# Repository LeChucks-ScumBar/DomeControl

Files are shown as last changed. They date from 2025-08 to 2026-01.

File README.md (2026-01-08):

# DomeControl
DomeControl for N.I.N.A
--------------------------

Kuppelsteuerung für das Großfeldteleskop in der Sternwarte Waldbröl (www.stsci.de)
------------------------
Status: Entwurf

anstehende Schritte:
 - Elektronik und Schalter montieren und anschließen
 - Test steurung mit N.I.N.A und Kuppel

 Software von:
 https://github.com/juanmb/ArduinoDomeController

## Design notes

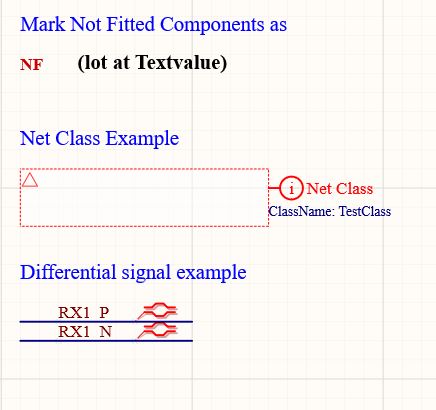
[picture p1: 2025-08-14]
Altium designe files/Bilder/Unbenannt.JPG

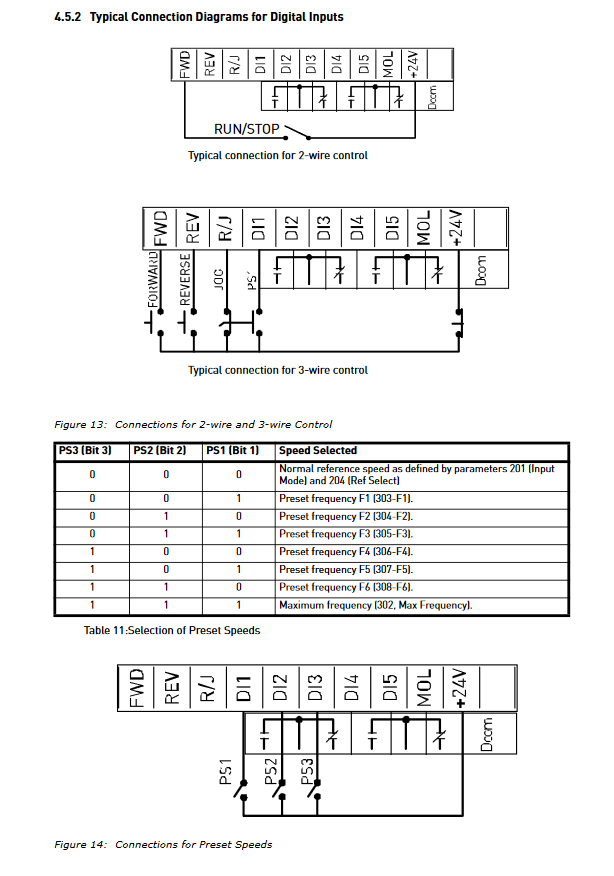
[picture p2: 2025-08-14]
Docs/Screenshot 2025-01-07 084854.png

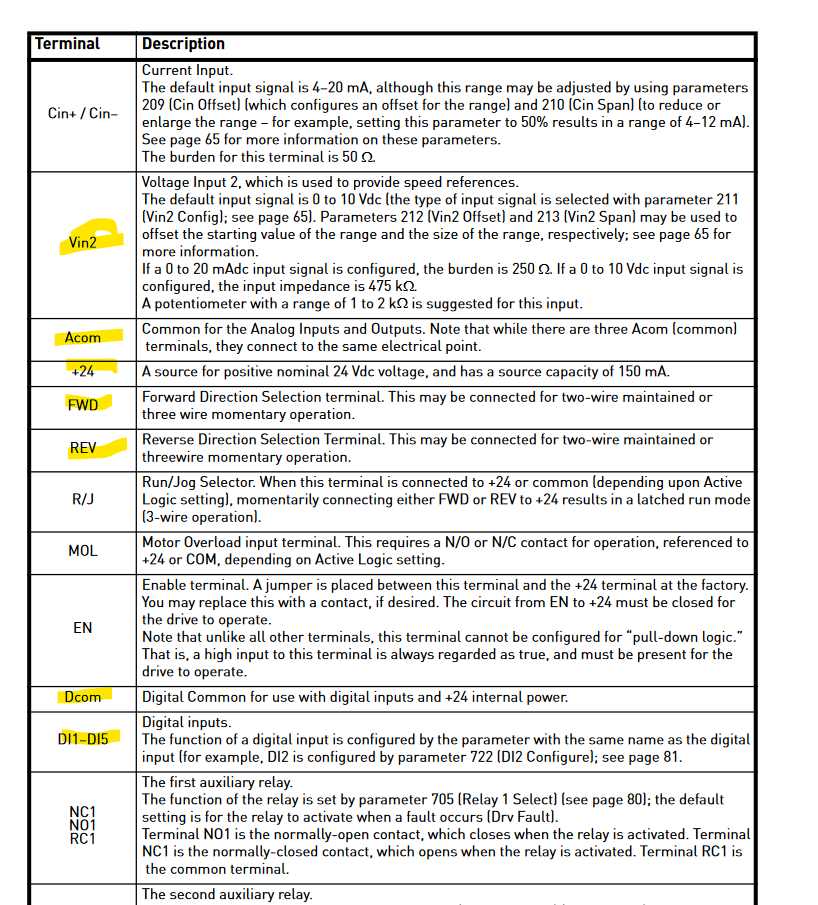
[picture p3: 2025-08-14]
Docs/Screenshot 2025-01-07 084709.png

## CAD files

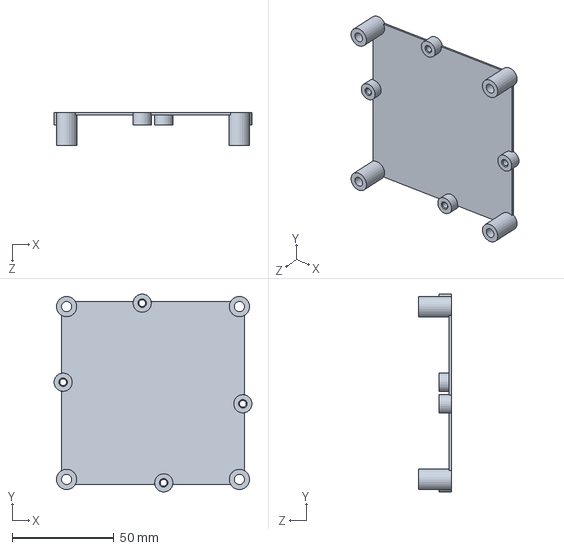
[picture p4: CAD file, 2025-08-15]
Solidworks/ArduinoBoxHalter/Case_oben.SLDPRT
97.4 x 97.4 x 16.0 mm

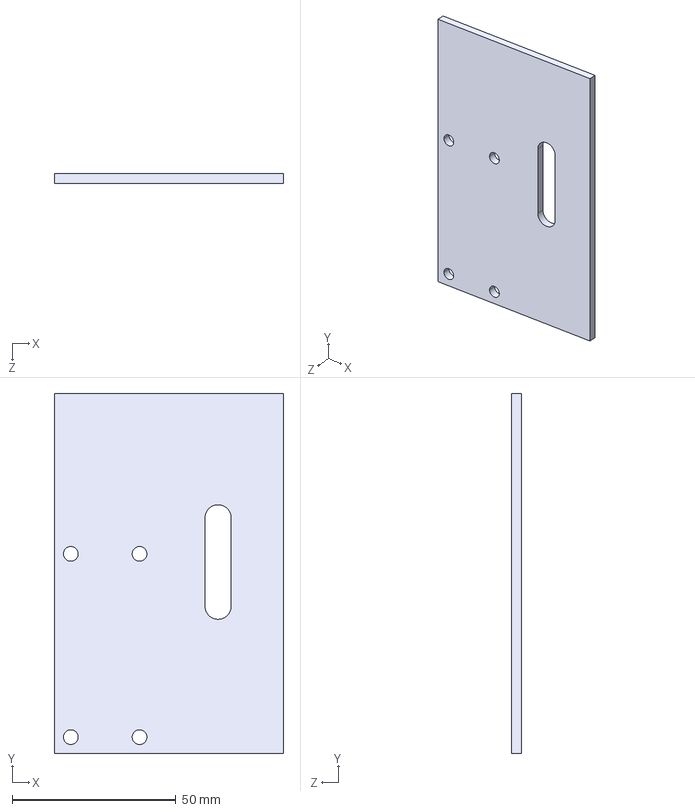
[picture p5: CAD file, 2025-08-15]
Solidworks/HomeTaster/HomeTaster.STEP
70.0 x 110.0 x 3.00 mm

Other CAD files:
Solidworks/ArduinoBoxHalter/Case_oben.STL
Solidworks/HomeTaster/HomeTaster.SLDDRW
Solidworks/HomeTaster/HomeTaster.SLDPRT

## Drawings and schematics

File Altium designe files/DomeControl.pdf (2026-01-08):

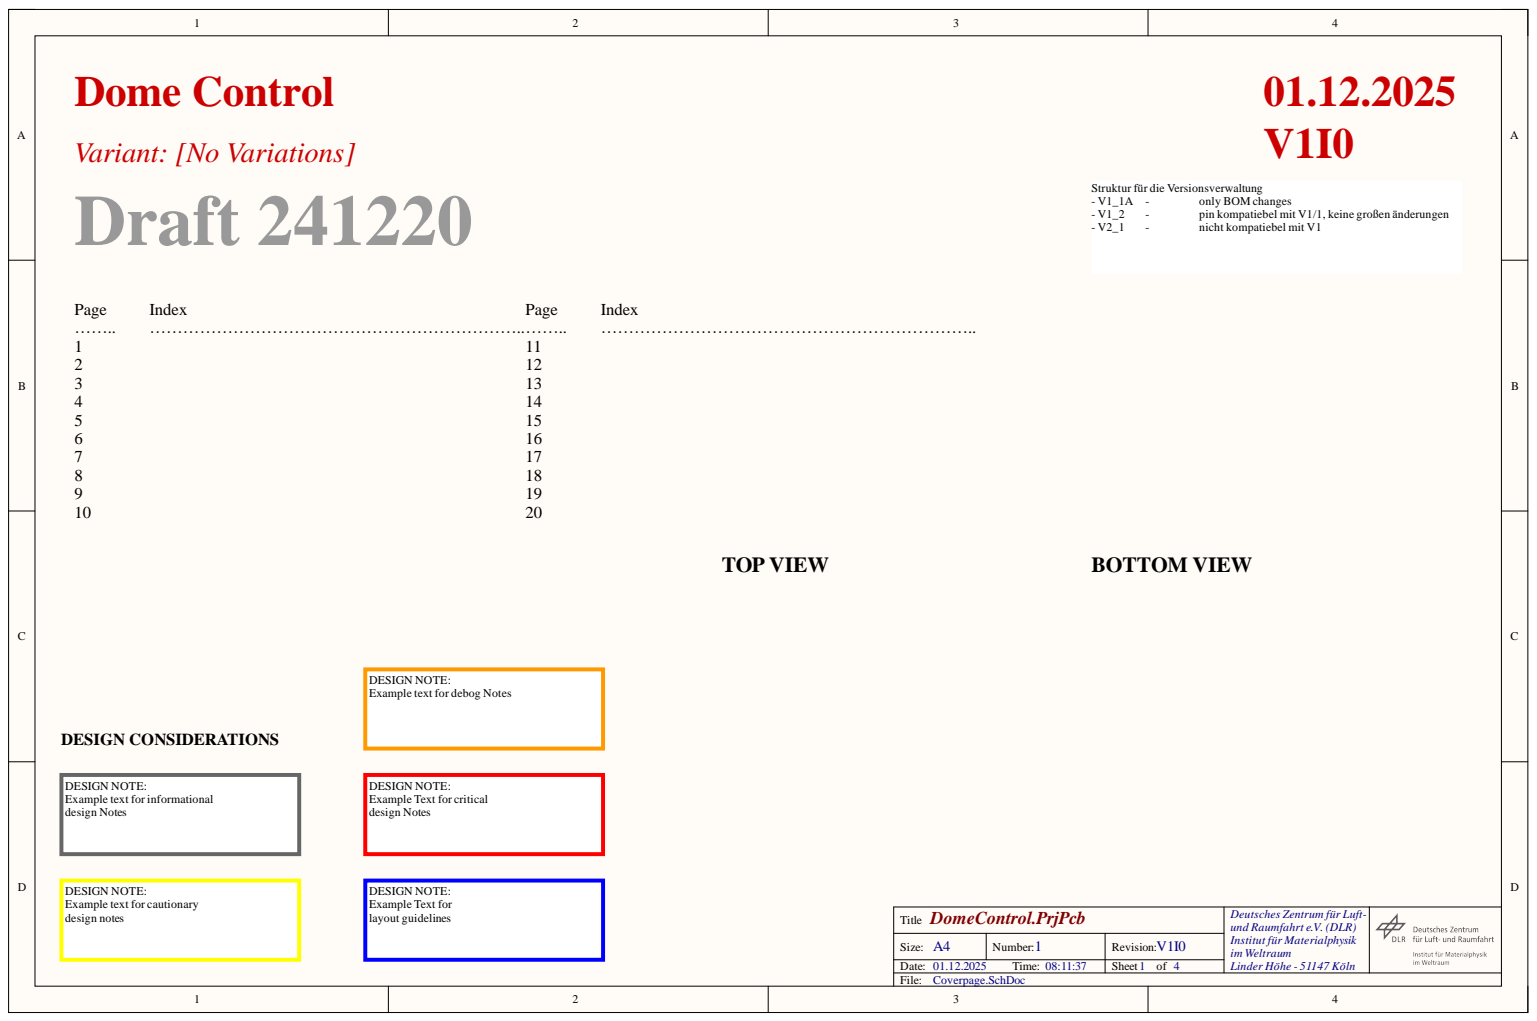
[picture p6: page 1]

Struktur für die Versionsverwaltung

DESIGN NOTE:
Example text for debog Notes

Example text for informational
design Notes

Example Text for critical

Example text for cautionary
design notes

Deutsches Zentrum für Luft-
und Raumfahrt e.V. (DLR)
Institut für Materialphysik
im Weltraum

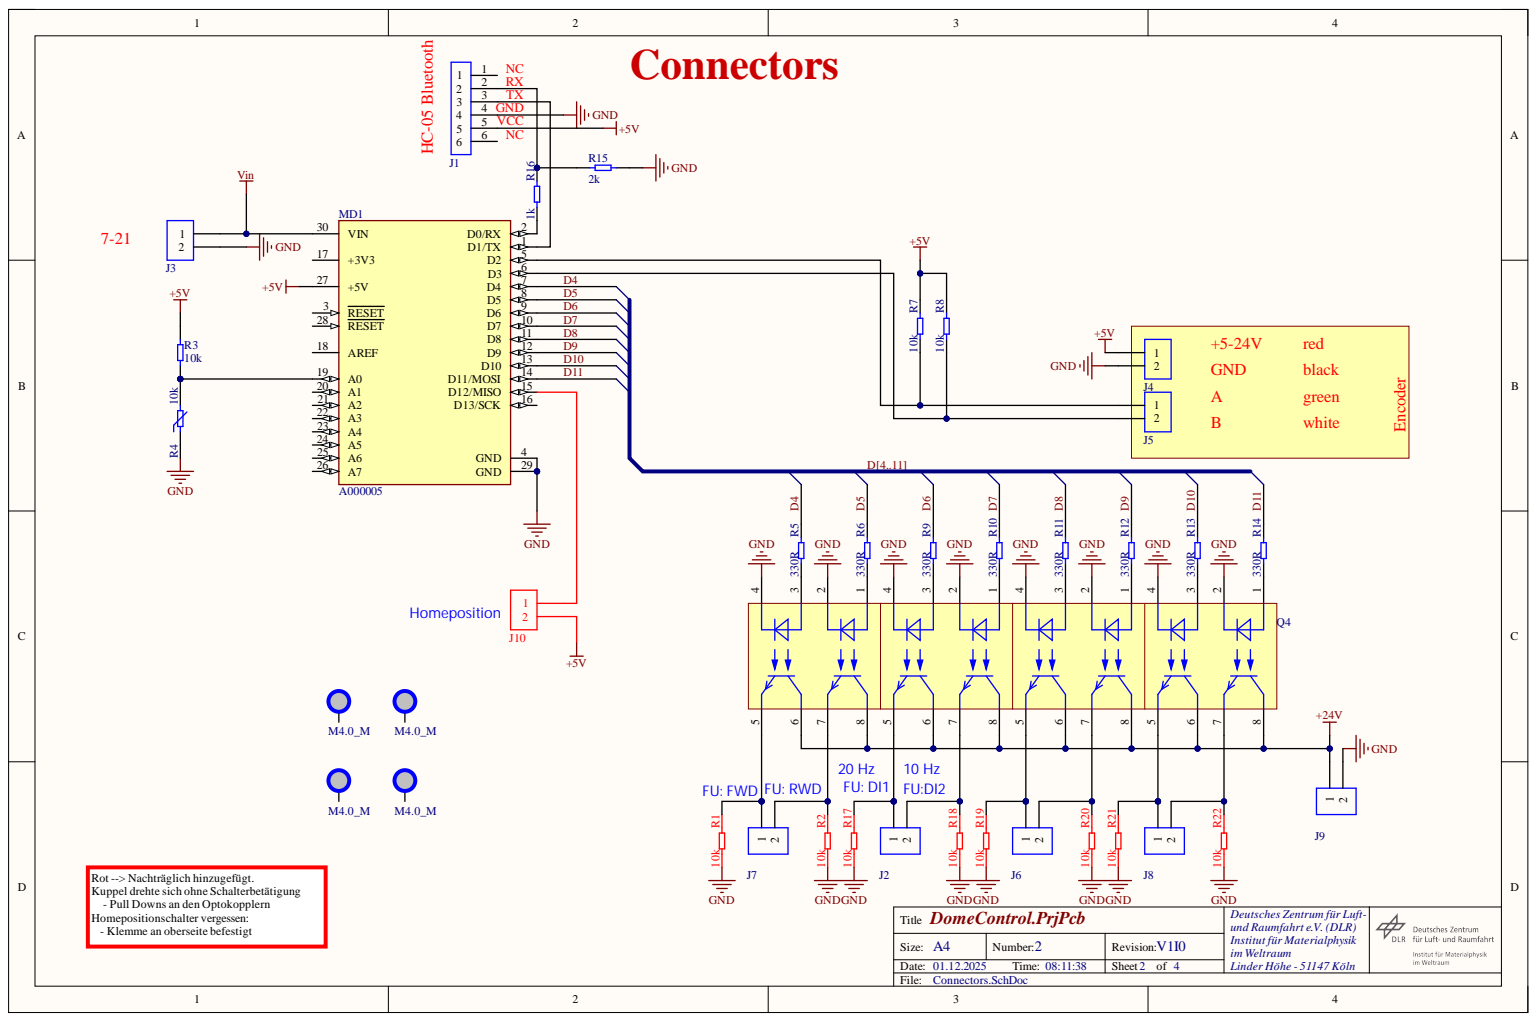
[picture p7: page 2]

Rot --> Nachträglich hinzugefügt.
Kuppel drehte sich ohne Schalterbetätigung
- Pull Downs an den Optokopplern
Homepositionschalter vergessen:
- Klemme an oberseite befestigt

Deutsches Zentrum für Luft-
und Raumfahrt e.V. (DLR)
Institut für Materialphysik
im Weltraum

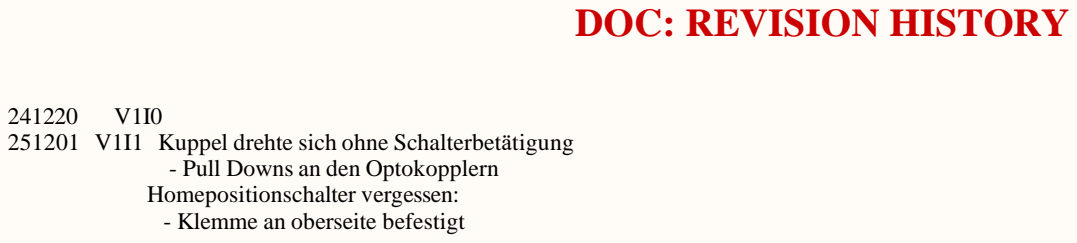
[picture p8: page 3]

251201 V1I1 Kuppel drehte sich ohne Schalterbetätigung

- Pull Downs an den Optokopplern
Homepositionschalter vergessen:
- Klemme an oberseite befestigt

Deutsches Zentrum für Luft-
und Raumfahrt e.V. (DLR)
Institut für Materialphysik
im Weltraum

DOC REVISION HISTORY.SchDoc

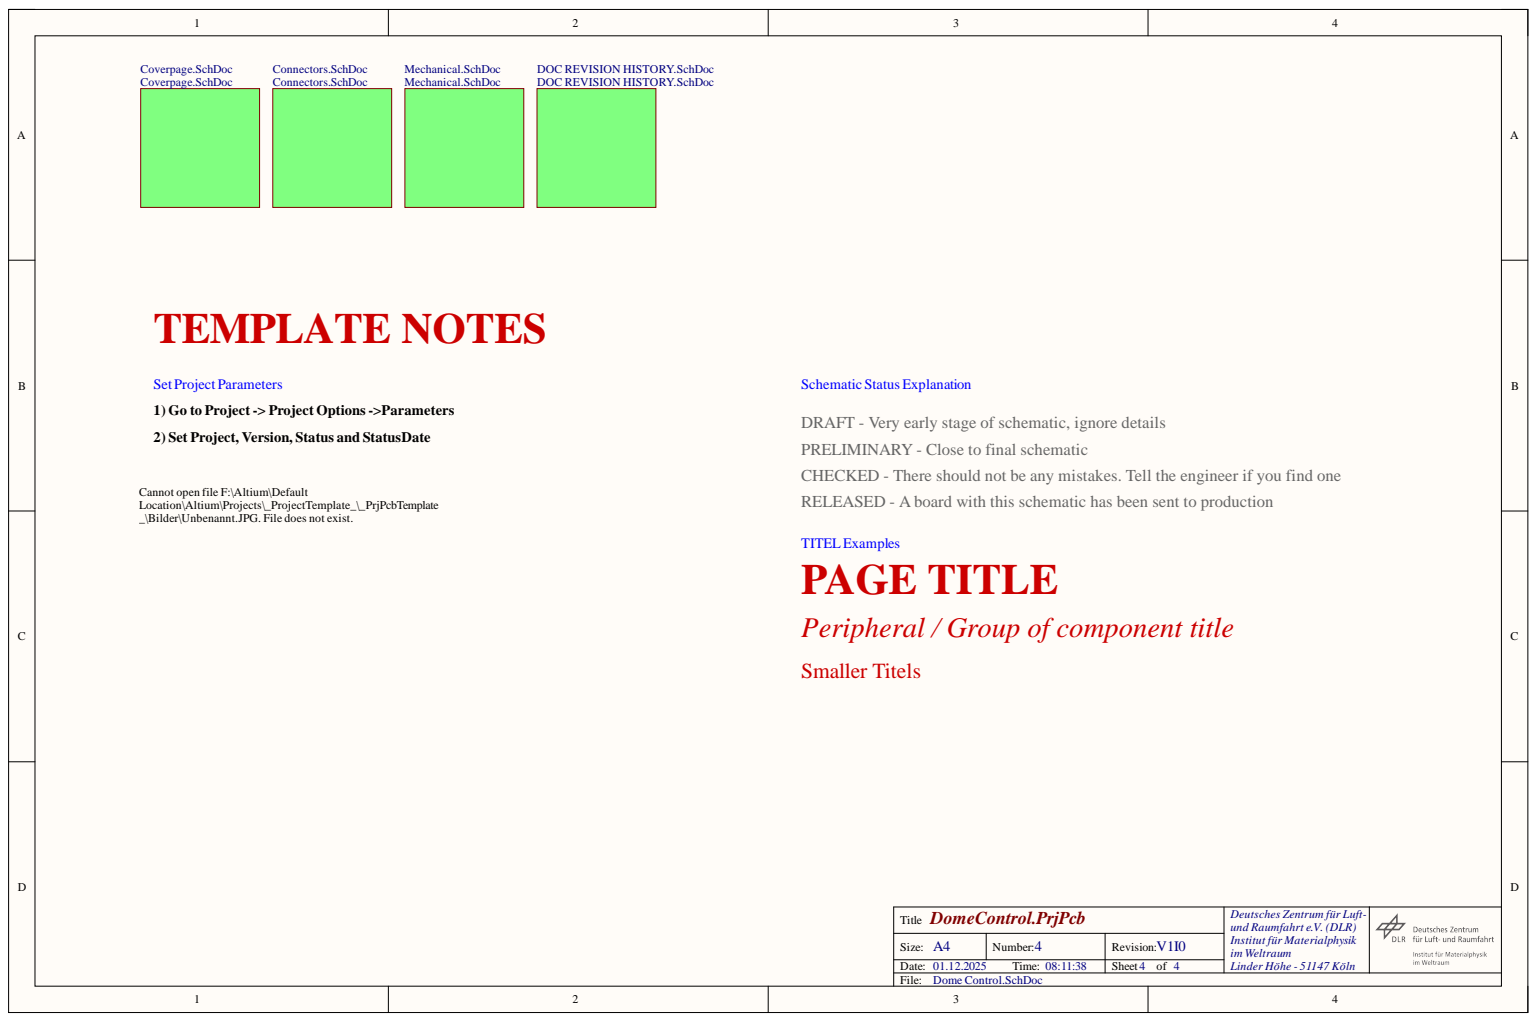
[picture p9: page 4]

DOC REVISION HISTORY.SchDoc

1) Go to Project -> Project Options ->Parameters

DRAFT - Very early stage of schematic, ignore details
PRELIMINARY - Close to final schematic
CHECKED - There should not be any mistakes. Tell the engineer if you find one

2) Set Project, Version, Status and StatusDate

RELEASED - A board with this schematic has been sent to production Cannot open file F:\Altium\Default
Location\Altium\Projects\_ProjectTemplate_\_PrjPcbTemplate
_\Bilder\Unbenannt.JPG. File does not exist.

Peripheral / Group of component title

Deutsches Zentrum für Luft-
und Raumfahrt e.V. (DLR)
Institut für Materialphysik
im Weltraum

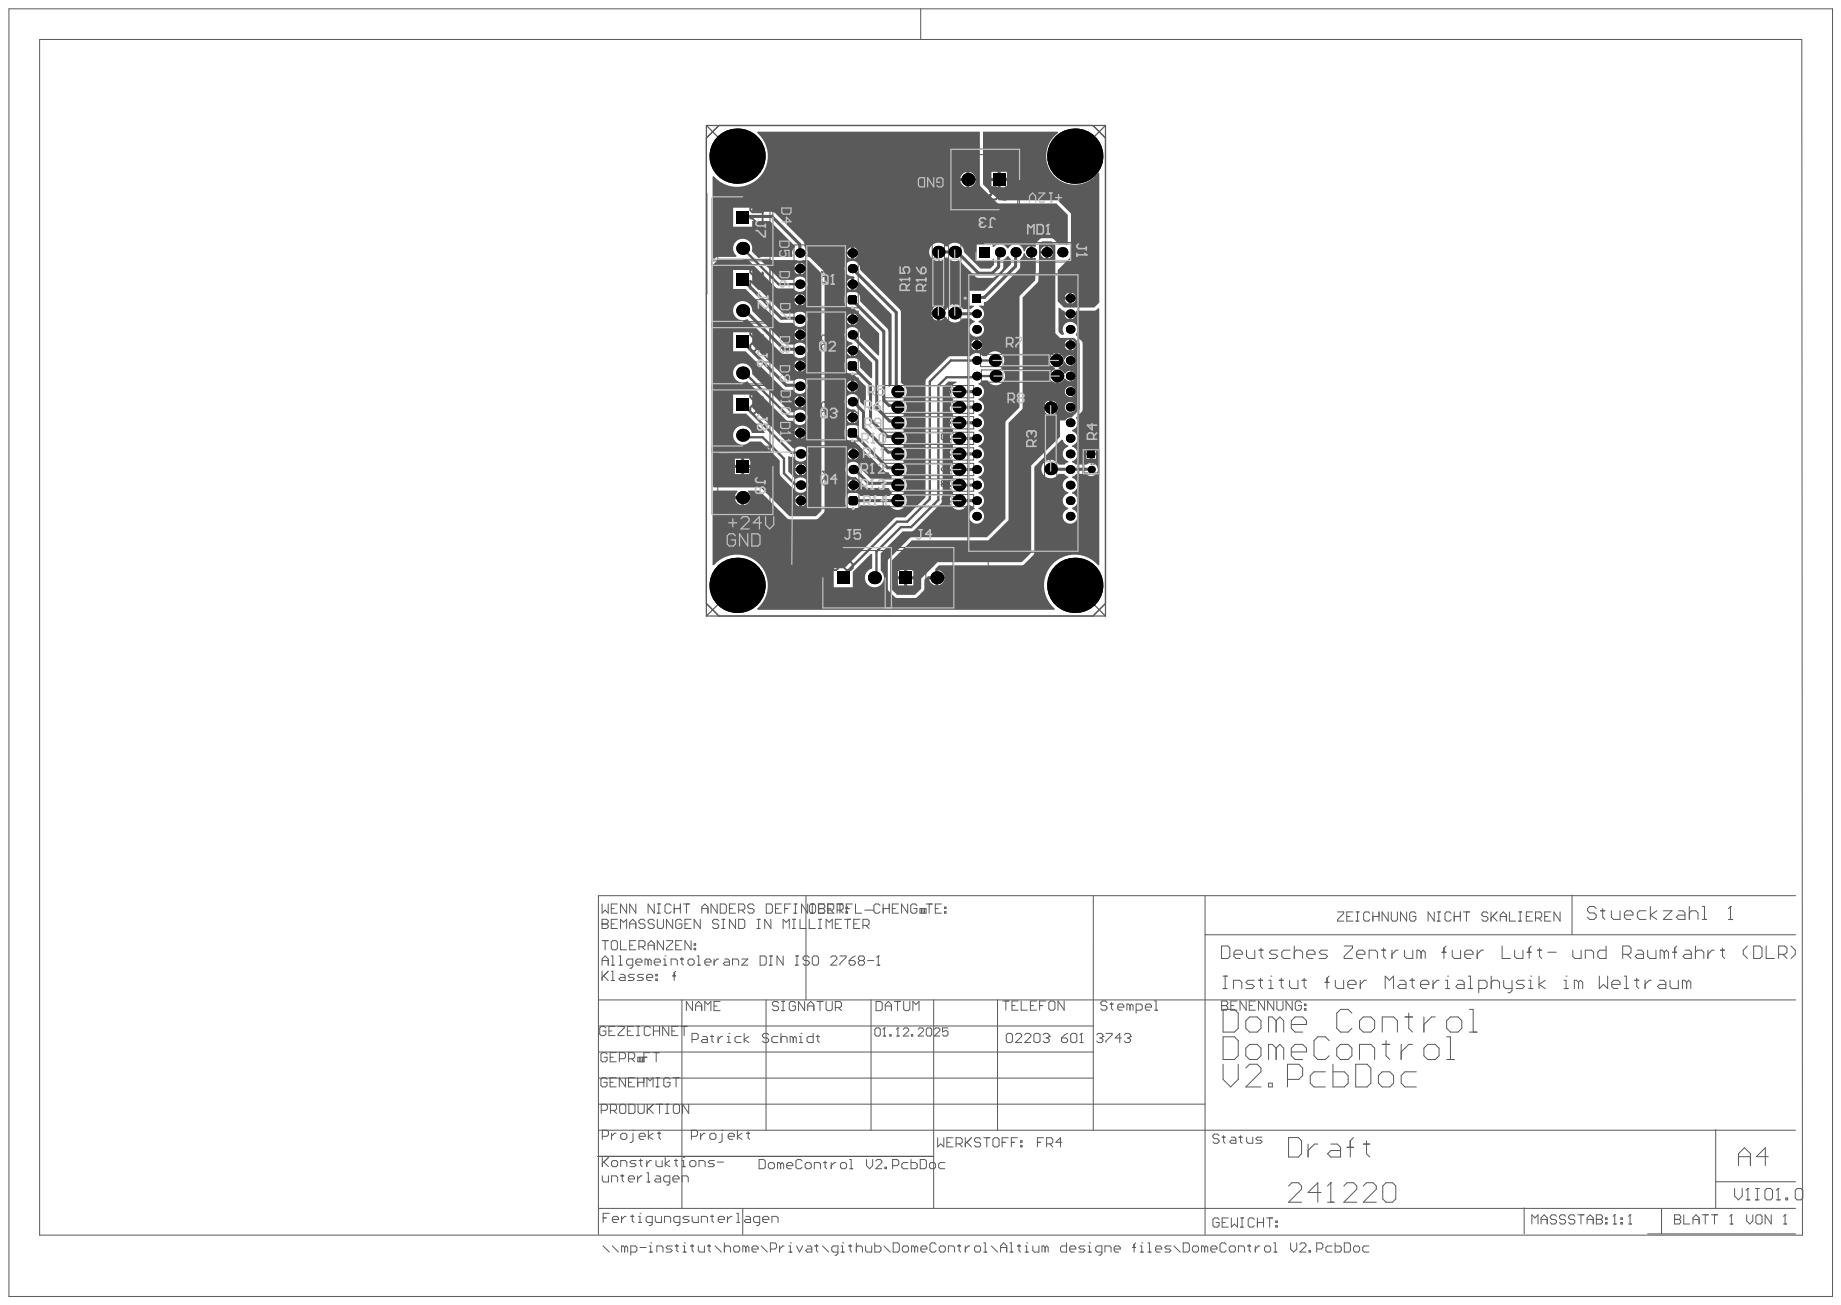
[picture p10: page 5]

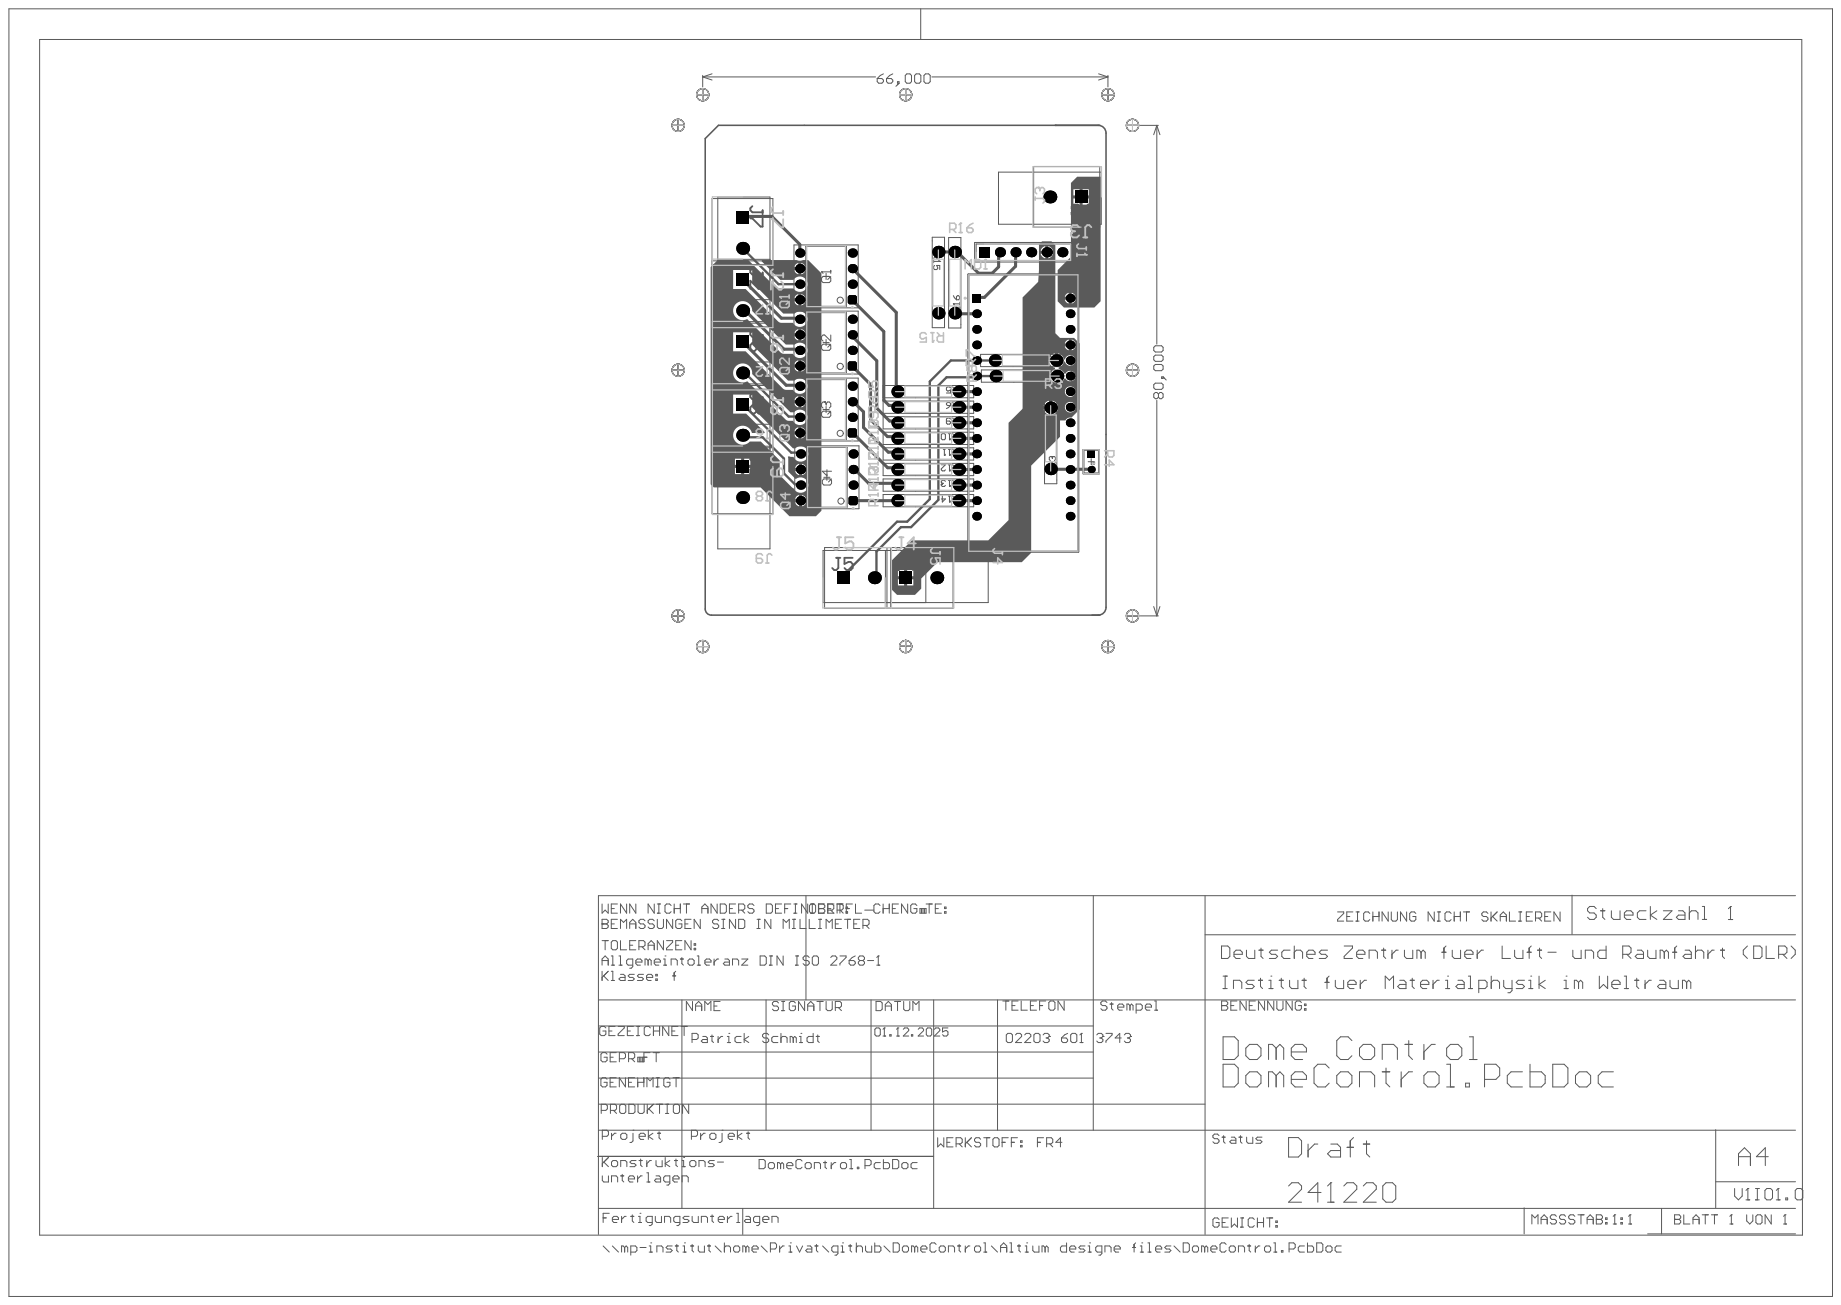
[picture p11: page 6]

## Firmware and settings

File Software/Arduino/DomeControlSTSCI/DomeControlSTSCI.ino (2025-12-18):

/*******************************************************************************
ArduinoDomeController
Azimuth control of an astronomical dome using Arduino


The MIT License

Copyright (C) 2017 Juan Menendez <juanmb@gmail.com>

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
THE SOFTWARE IS PROVIDED "AS IS", WITHOUT WARRANTY OF ANY KIND, EXPRESS OR
IMPLIED, INCLUDING BUT NOT LIMITED TO THE WARRANTIES OF MERCHANTABILITY,
  FITNESS FOR A PARTICULAR PURPOSE AND NONINFRINGEMENT. IN NO EVENT SHALL THE
  AUTHORS OR COPYRIGHT HOLDERS BE LIABLE FOR ANY CLAIM, DAMAGES OR OTHER
  LIABILITY, WHETHER IN AN ACTION OF CONTRACT, TORT OR OTHERWISE, ARISING FROM,
  OUT OF OR IN CONNECTION WITH THE SOFTWARE OR THE USE OR OTHER DEALINGS IN
  THE SOFTWARE.
*******************************************************************************/

#include <EEPROM.h>
#include <avr/wdt.h>
#include <SoftwareSerial.h>
#include "MonsterMotorShield.h"
#include "serial_command.h"


// Configuration
//#define HAS_SHUTTER     // Uncomment if the shutter controller is available
//#define MOTOR_SHIELD  // Uncomment if the motor driver is a Monster Motor Shield
//#define USE_BUTTONS   // Uncomment if you want to move the dome with push buttons

#define AZ_TIMEOUT      30000   // Azimuth movement timeout (in ms)
#define AZ_TOLERANCE    46      	// Azimuth target tolerance in encoder ticks    //----------------------------------------------------- change from 4 to 40
#define AZ_SLOW_RANGE   200       // The motor will run at slower speed when the
                                // dome is at this number of ticks from the target

// pin definitions
#define ENCODER1 2      // Encoder A
#define ENCODER2 3      // Encoder B
#define HOME_SENSOR 12  // Home sensor (active low)
//#define BUTTON_CW   11  // CW movement button (active low)  ----------------
//#define BUTTON_CCW  12  // CCW movement button (Active low) ---------------

#ifdef HAS_SHUTTER
#ifdef MOTOR_SHIELD
#error "HAS_SHUTTER and MOTOR_SHIELD cannot be defined at the same time"
#endif

// pins of HC12 module (serial radio transceiver)
//#define HC12_RX 2       // Receive Pin on HC12
//#define HC12_TX 1      // Transmit Pin on HC12
#endif

// motor pins (if not using the Monster Motor Shield)
#ifndef MOTOR_SHIELD
#define MOTOR_JOG 8     // Motor jog mode (low speed)
#define MOTOR_CW 5      // Move motor clockwise fast
#define MOTOR_CCW 4     // Move motor counterclockwise fast
#define MOTOR_CW_slow 5      // Move motor clockwise slow
#define MOTOR_CCW_slow 4     // Move motor counterclockwise slow
#define fast_fu 6
#define slow_fu 7
#endif

#define FIX_Ticks_PER_TURN 7167
// Message Destination
#define TO_MAXDOME  0x00
#define TO_COMPUTER 0x80

#define VBAT_FACTOR (5.0/1024.0)
#define VBAT_OFFSET 10.55

#define BAUDRATE 19200

// Commands
#define ABORT_CMD   0x03 // Abort azimuth movement
#define HOME_CMD    0x04 // Move until 'home' position is detected
#define GOTO_CMD    0x05 // Go to azimuth position
#define SHUTTER_CMD 0x06 // Send a command to shutter
#define STATUS_CMD  0x07 // Retrieve status
#define TICKS_CMD   0x09 // Set the number of tick per revolution of the dome
#define ACK_CMD     0x0A // ACK (?)
#define SETPARK_CMD 0x0B // Set park coordinates and shutter closing policy
#define VBAT_CMD    0x0C // Read shutter's battery voltage

// Shutter commands
#define OPEN_SHUTTER            0x01
#define OPEN_UPPER_ONLY_SHUTTER 0x02
#define CLOSE_SHUTTER           0x03
#define EXIT_SHUTTER            0x04 // Command sent to shutter on program exit
#define ABORT_SHUTTER           0x07

#define DIR_CW  0x01
#define DIR_CCW 0x02

// EEPROM addresses
#define ADDR_PARK_POS           0
#define ADDR_TICKS_PER_TURN     2
#define ADDR_PARK_ON_SHUTTER    4


enum MotorSpeed { MOTOR_STOP, MOTOR_SLOW, MOTOR_FAST };

enum AzimuthEvent {
    EVT_NONE,
    EVT_GOTO,
    EVT_HOME,
    EVT_ABORT
};

enum AzimuthStatus {
    ST_IDLE,
    ST_MOVING,
    ST_APPROACHING,
    ST_HOMING,
    ST_ERROR,
};

// MaxDome II azimuth status
enum MDAzimuthStatus {
    AS_IDLE = 1,
    AS_MOVING_CW,
    AS_MOVING_CCW,
    AS_IDLE2,
    AS_ERROR
};

// MaxDome II shutter status
enum ShutterStatus {
    SS_CLOSED = 0,
    SS_OPENING,
    SS_OPEN,
    SS_CLOSING,
    SS_ABORTED,
    SS_ERROR
};


#ifdef HAS_SHUTTER
// Create a Software Serial Port to communicate with the shutter controller
//SoftwareSerial HC12(HC12_TX, HC12_RX);
#endif

SerialCommand sCmd;

#ifdef MOTOR_SHIELD
Motor motor(0);
#endif

bool park_on_shutter = false;
bool home_reached = false;
bool parking = false;
uint8_t current_dir = DIR_CW;   // Current azimuth movement direction
uint16_t park_pos = 0;          // Parking position                     -------------------------- hier noch anpassen
uint16_t current_pos = 0;       // Current dome position
uint16_t target_pos = 0;        // Target dome position
uint16_t home_pos = 0;          // Home position                        -------------------------- hier noch anpassen
uint16_t ticks_per_turn =  FIX_Ticks_PER_TURN; //7167;  // Encoder ticks per dome revolution  --------------------------hier Ticks für 360° umdrehung
AzimuthStatus state = ST_IDLE;
AzimuthEvent az_event = EVT_NONE;

uint16_t encoderPinALast = LOW;
uint16_t encoderPinANow = LOW;

// Convert two bytes to a uint16_t value (big endian)
uint16_t bytesToInt(uint8_t *data)
{
    uint16_t value1 = data[1];
    uint16_t value2 = data[0];
    return (value1 & 0xff) | ((value2 << 8) & 0xff00);
}

// Convert a uint16_t value to bytes (big endian)
void intToBytes(uint16_t value, uint8_t *data)
{
    data[1] = value & 0xff;
    data[0] = (value >> 8) & 0xff;
}

// Read a uint16_t value from EEPROM (little endian)
uint16_t eepromReadUint16(int address)
{
    uint16_t value1 = EEPROM.read(address);
    uint16_t value2 = EEPROM.read(address + 1);
    return (value1 & 0xff) | ((value2 << 8) & 0xff00);
}

// Read a uint16_t value from EEPROM (little endian)
void eepromWriteUint16(int address, uint16_t value)
{
    uint8_t value1 = value & 0xff;
    uint8_t value2 = (value >> 8) & 0xff;
    EEPROM.write(address, value1);
    EEPROM.write(address + 1, value2);
}


// Obtain the direction of the shortest path between two positons
uint8_t getDirection(uint16_t current, uint16_t target)
{
    if (target > current)
        return ((target - current) > ticks_per_turn / 2) ? DIR_CCW : DIR_CW;

    return ((current - target) > ticks_per_turn / 2) ? DIR_CW : DIR_CCW;
}

// Obtain the distance between two positons
uint16_t getDistance(uint16_t current, uint16_t target)
{
    // obtain the absolute value of the difference
    uint16_t diff = (target > current) ?  target - current : current - target;

    if (diff > ticks_per_turn / 2)
        return ticks_per_turn - diff;

    return diff;
}

inline void moveAzimuth(uint8_t dir, bool slow)
{
    digitalWrite(LED_BUILTIN, HIGH);
#ifdef MOTOR_SHIELD
    int speed = slow ? 800 : 1023;
    motor.run(dir == DIR_CW, speed);
#else
    if(dir == true)
    {
        digitalWrite(MOTOR_CW_slow, true);
        digitalWrite(MOTOR_CCW_slow, false);
    }else
    {
        
        digitalWrite(MOTOR_CW_slow, false);
        digitalWrite(MOTOR_CCW_slow, true);
    }
    if(slow)
    {
        digitalWrite(fast_fu, false);
        digitalWrite(slow_fu, true);
    }
    else
    {
      
        digitalWrite(fast_fu, true);
        digitalWrite(slow_fu, false);
      
    }


#endif
}

inline void stopAzimuth()
{
    digitalWrite(LED_BUILTIN, LOW);
#ifdef MOTOR_SHIELD
    motor.stop();
#else
    digitalWrite(MOTOR_JOG, LOW);
    digitalWrite(MOTOR_CW, LOW);
    digitalWrite(MOTOR_CCW, LOW);
    digitalWrite(MOTOR_CW_slow, LOW);
    digitalWrite(MOTOR_CCW_slow, LOW);
    digitalWrite(fast_fu, false);
    digitalWrite(slow_fu, false);
#endif
}

float getShutterVBat()
{
    int adc = 0;

#ifdef HAS_SHUTTER
    char buffer[5];

    HC12.flush();
    for (int i = 0; i < 4; i++) {
        HC12.println("vbat");
        delay(100);

        if (HC12.read() == 'v') {
            for (int j = 0; j < 4; j++) {
                buffer[j] = HC12.read();
            }

            buffer[4] = 0;
            adc = atoi(buffer);
            break;
        }
    }
#endif

    // Convert ADC reading to voltage
    return (float)adc * VBAT_FACTOR + VBAT_OFFSET;
}

ShutterStatus getShutterStatus()
{
    ShutterStatus st = SS_OPEN;

#ifdef HAS_SHUTTER
    st = SS_ERROR;
    HC12.flush();
    for (int i = 0; i < 4; i++) {
        HC12.println("stat");
        delay(100);

        char c = 0;
        while (HC12.available() > 0) {
            c = HC12.read();
        }

        if (c >= '0' && c <= ('0' + SS_ERROR)) {
            st = (ShutterStatus)(c - '0');
            break;
        }
    }
#endif
    return st;
}


void cmdAbort(uint8_t *cmd)
{
#ifdef HAS_SHUTTER
    HC12.println("abort");  // abort shutter movement
#endif

    az_event = EVT_ABORT;

    uint8_t resp[] = {START, 2, TO_COMPUTER | ABORT_CMD, 0x00};
    sCmd.sendResponse(resp, 4);
}

void cmdHomeAzimuth(uint8_t *cmd)
{
    if (!parking) {
        current_dir = getDirection(current_pos, 0);
        az_event = EVT_HOME;
    }

    uint8_t resp[] = {START, 3, TO_COMPUTER | HOME_CMD, 0x01, 0x00};
    sCmd.sendResponse(resp, 5);
}

void cmdGotoAzimuth(uint8_t *cmd)
{
    if (!parking) {
        current_dir = cmd[3];
        target_pos = bytesToInt(cmd + 4);
        az_event = EVT_GOTO;
    }

    uint8_t resp[] = {START, 3, TO_COMPUTER | GOTO_CMD, 0x01, 0x00};
    sCmd.sendResponse(resp, 5);
}

void parkDome()
{
    parking = true;
    target_pos = park_pos;
    az_event = EVT_GOTO;
}

void cmdShutterCommand(uint8_t *cmd)
{
#ifdef HAS_SHUTTER
    switch(cmd[3]) {
    case OPEN_SHUTTER:
        HC12.println("open");
        break;
    case OPEN_UPPER_ONLY_SHUTTER:
        HC12.println("open1");
        break;
    case CLOSE_SHUTTER:
        if (park_on_shutter)
            parkDome();
        else
            HC12.println("close");
        break;
    case EXIT_SHUTTER:
        HC12.println("exit");
        break;
    case ABORT_SHUTTER:
        HC12.println("abort");
        break;
    }
#endif

    uint8_t resp[] = {START, 2, TO_COMPUTER | SHUTTER_CMD, 0x00};
    sCmd.sendResponse(resp, 4);
}

void cmdStatus(uint8_t *cmd)
{
    MDAzimuthStatus az_status;
    if (state == ST_IDLE) {
        az_status = AS_IDLE;
    }
    else if (state == ST_ERROR) {
        az_status = AS_ERROR;
    }
    else {
        if (current_dir == DIR_CW)
            az_status = AS_MOVING_CW;
        else
            az_status = AS_MOVING_CCW;
    }

    uint8_t sh_status = (uint8_t)getShutterStatus();
    uint8_t resp[] = {START, 9, TO_COMPUTER | STATUS_CMD, sh_status, az_status,
                      0x00, 0x00, 0x00, 0x00, 0x00, 0x00
                     };

    intToBytes(current_pos, resp + 5);
    intToBytes(home_pos, resp + 7);

    sCmd.sendResponse(resp, 11);
}

void cmdSetPark(uint8_t *cmd)
{
    park_on_shutter = cmd[3];
    park_pos = bytesToInt(cmd + 4);

    EEPROM.write(ADDR_PARK_ON_SHUTTER, park_on_shutter);
    eepromWriteUint16(ADDR_PARK_POS, park_pos);

    uint8_t resp[] = {START, 2, TO_COMPUTER | SETPARK_CMD, 0x00};
    sCmd.sendResponse(resp, 4);
}

void cmdSetTicks(uint8_t *cmd)
{
    ticks_per_turn = bytesToInt(cmd + 3);
    eepromWriteUint16(ADDR_TICKS_PER_TURN, ticks_per_turn);

    uint8_t resp[] = {START, 2, TO_COMPUTER | TICKS_CMD, 0x00};
    sCmd.sendResponse(resp, 4);
}

void cmdVBat(uint8_t *cmd)
{
    uint8_t resp[] = {START, 4, TO_COMPUTER | VBAT_CMD, 0x00, 0x00, 0x00};

    int vbat = getShutterVBat() * 100;
    intToBytes(vbat, resp + 3);

    sCmd.sendResponse(resp, 6);
}

void cmdAck(uint8_t *cmd)
{
    uint8_t resp[] = {START, 3, TO_COMPUTER | ACK_CMD, 0x03, 0x00};
    sCmd.sendResponse(resp, 5);
}

void updateAzimuthFSM()
{
    static unsigned long t0;

    switch(state) {
    case ST_HOMING:
        if (az_event == EVT_ABORT) {
            parking = false;
            stopAzimuth();
            state = ST_IDLE;
        }
        else if (home_reached) {
            stopAzimuth();
            state = ST_IDLE;
            home_reached = false;
        }
        else if (millis() - t0 > AZ_TIMEOUT) {
            stopAzimuth();
            state = ST_ERROR;
        }
        break;

    case ST_MOVING:
        if (az_event == EVT_ABORT) {
            parking = false;
            stopAzimuth();
            state = ST_IDLE;
        }
        else if (getDistance(current_pos, target_pos) < AZ_SLOW_RANGE) {
            moveAzimuth(current_dir, true);
            state = ST_APPROACHING;
        }
        else if (millis() - t0 > AZ_TIMEOUT) {
            stopAzimuth();
            state = ST_ERROR;
        }
        break;

    case ST_APPROACHING:
        if (az_event == EVT_ABORT) {
            parking = false;
            stopAzimuth();
            state = ST_IDLE;
        }
        else if (getDistance(current_pos, target_pos) < AZ_TOLERANCE) {
            stopAzimuth();

            // close shutter after parking
            if (parking) {
                parking = false;
#ifdef HAS_SHUTTER
                HC12.println("close");
#endif
            }

            state = ST_IDLE;
        }
        else if (millis() - t0 > AZ_TIMEOUT) {
            stopAzimuth();
            state = ST_ERROR;
        }
        break;

    case ST_ERROR:
    case ST_IDLE:
        if (az_event == EVT_HOME) {
            t0 = millis();
            state = ST_HOMING;
            moveAzimuth(current_dir, false);
        }
        else if (az_event == EVT_GOTO) {
            t0 = millis();
            state = ST_MOVING;
            moveAzimuth(current_dir, false);
        }
        break;
    }
    az_event = EVT_NONE;
}

int oldEnc1;
// Encoder interrupt service routine
void encoderISR()
{

encoderPinANow = digitalRead(ENCODER1);

  if ((encoderPinALast == HIGH) && (encoderPinANow == LOW)) {
    if (digitalRead(ENCODER2) == HIGH) {
              if (current_pos >= ticks_per_turn - 1)
            current_pos = 0;
        else
            current_pos++;
    } else {
      if (current_pos == 0)
            current_pos = ticks_per_turn - 1;
        else
            current_pos--;
    }
  }
  encoderPinALast = encoderPinANow;
    /*
    if(digitalRead(ENCODER1) == digitalRead(ENCODER2)) {
        if (current_pos == 0)
            current_pos = ticks_per_turn - 1;
        else
            current_pos--;
    }
    else {
        if (current_pos >= ticks_per_turn - 1)
            current_pos = 0;
        else
            current_pos++;
    }*/
}

void setup()
{
    wdt_disable();
    wdt_enable(WDTO_2S);

    sCmd.addCommand(ABORT_CMD, 2, cmdAbort);
    sCmd.addCommand(HOME_CMD, 2, cmdHomeAzimuth);
    sCmd.addCommand(GOTO_CMD, 5, cmdGotoAzimuth);
    sCmd.addCommand(SHUTTER_CMD, 3, cmdShutterCommand);
    sCmd.addCommand(STATUS_CMD, 2, cmdStatus);
    sCmd.addCommand(SETPARK_CMD, 5, cmdSetPark);
    sCmd.addCommand(TICKS_CMD, 4, cmdSetTicks);
    sCmd.addCommand(ACK_CMD, 2, cmdAck);
    sCmd.addCommand(VBAT_CMD, 2, cmdVBat);
    pinMode(LED_BUILTIN, OUTPUT);
    pinMode(HOME_SENSOR, INPUT_PULLUP);
    
    pinMode(ENCODER1, INPUT_PULLUP);
    
    pinMode(ENCODER2, INPUT_PULLUP);
 //   pinMode(BUTTON_CW, INPUT_PULLUP);
 //   pinMode(BUTTON_CCW, INPUT_PULLUP);

#ifndef MOTOR_SHIELD
    pinMode(MOTOR_JOG, OUTPUT);
    pinMode(MOTOR_CW, OUTPUT);
    pinMode(MOTOR_CCW, OUTPUT);
    pinMode(MOTOR_CW_slow, OUTPUT);
    pinMode(MOTOR_CCW_slow, OUTPUT);
    pinMode(fast_fu, OUTPUT);
    pinMode(slow_fu, OUTPUT);
    
#endif

    attachInterrupt(digitalPinToInterrupt(ENCODER1), encoderISR, CHANGE);

    park_pos = eepromReadUint16(ADDR_PARK_POS);
    park_on_shutter = EEPROM.read(ADDR_PARK_ON_SHUTTER);
    ticks_per_turn = FIX_Ticks_PER_TURN; //eepromReadUint16(ADDR_TICKS_PER_TURN);

    Serial.begin(19200);
    Serial.println("hello there2");
    
#ifdef HAS_SHUTTER
    HC12.begin(9600);   // Open serial port to HC12
#endif
}

// move the motor when the buttons are pressed

void read_buttons()
{
   /* static int prev_cw_button = 0, prev_ccw_button = 0;
    int cw_button = !digitalRead(BUTTON_CW);
    int ccw_button = !digitalRead(BUTTON_CCW);

    if (cw_button != prev_cw_button) {
        if (cw_button) {
            digitalWrite(LED_BUILTIN, HIGH);
	    moveAzimuth(DIR_CW, false);
        }
        else {
            digitalWrite(LED_BUILTIN, LOW);
	    stopAzimuth();
        }
    }
    else if (ccw_button != prev_ccw_button) {
        if (ccw_button) {
            digitalWrite(LED_BUILTIN, HIGH);
	    moveAzimuth(DIR_CCW, false);
        }
        else {
            digitalWrite(LED_BUILTIN, LOW);
	    stopAzimuth();
        }
    }
    prev_cw_button = cw_button;
    prev_ccw_button = ccw_button;*/
}



void loop()
{
    sCmd.readSerial();
    updateAzimuthFSM();
#ifdef USE_BUTTONS
    read_buttons();
#endif
    wdt_reset();

    // store detected home position
    if (!digitalRead(HOME_SENSOR)) {
        if (state == ST_HOMING) {
            home_pos = 0;
            current_pos = 0;
            home_reached = true;
            Serial.println("home");
        }
        else
            home_pos = current_pos;
    }
/*

    }}*/
}

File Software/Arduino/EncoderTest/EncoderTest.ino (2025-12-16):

// pin definitions
#define ENCODER1 2      // Encoder A
#define ENCODER2 3      // Encoder B
#define HOME_SENSOR 12

int encoderPinA = ENCODER1;
int encoderPinB = ENCODER2;
uint16_t encoderPos0 = 0;
unsigned long encoderPos1 = 0;
double encoderPos2 = 0;

uint16_t encoderPos00 = 10000;
unsigned long encoderPos11 = 10000;
double encoderPos22 = 10000;
int encoderPinALast = LOW;
int encoderPinANow = LOW;

char buf[100];

bool state = false;

void setup() {
  pinMode (encoderPinA, INPUT_PULLUP);
  pinMode (encoderPinB, INPUT_PULLUP);
   pinMode (HOME_SENSOR, INPUT_PULLUP);
  Serial.begin (115200);
}

void loop() {
  encoderPinANow = digitalRead(encoderPinA);
  if ((encoderPinALast == HIGH) && (encoderPinANow == LOW)) {
    if (digitalRead(encoderPinB) == HIGH) {
      encoderPos0++;
      encoderPos1++;
      encoderPos2 +=1;
    } else {
      encoderPos0--;
      encoderPos1--;
      encoderPos2+=1;
    }
    sprintf(buf, "Pos_u16: %d\tPos_U32: %d\tPos_float: %f.0", encoderPos0, encoderPos1,encoderPos2);
    Serial.println(buf);
    //Serial.println(encoderPos);
  }
  encoderPinALast = encoderPinANow;

      // store detected home position
    if (!digitalRead(HOME_SENSOR)) {
        if (state == true) {
 
 encoderPos00 = encoderPos0;
 encoderPos11 = encoderPos1;
encoderPos22 = encoderPos2;
            encoderPos0 = 0;
            encoderPos1 = 0;
            encoderPos2 = 0;
            state = false;
            Serial.println("home");
    sprintf(buf, "maxPos_u16: %d\tmaxPos_U32: %d\tmaxPos_float: %f.0", encoderPos00, encoderPos11,encoderPos22);
    Serial.println(buf);

        }
    }else if (digitalRead(HOME_SENSOR)) 
    {
      state = true;
    }

    
}

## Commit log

2025-08-14 Status Entwurf
    [Connectors.SchDoc, Coverpage.SchDoc, DOC REVISION HISTORY.SchDoc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]
2025-08-15 Add files via upload
    add stl parts
    [Case_oben.SLDPRT, Case_oben.STL, HomeTaster.SLDDRW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]
2025-08-15 Add arduino files
2025-08-15 Add driver links
2025-11-30 Change ticks per resolution (ticks pro Umdrehung) auf 7800
    Wert muss noch genau ermittelt wwerden.
    Tolerenz wurde von 4 auf 86 Ticks erhöht - Diesen Wert auch noch anpassen 4° entspechen 86 TIcks
    Wert für Home- und Parkposition festlegen
2025-12-01 Update schematic
    Pullups hinzugefügt und Homesensor
    [Connectors.SchDoc, DOC REVISION HISTORY.SchDoc]
2025-12-16 set ticks_per_turn from 7800 to 7167 Add encoder Test program
2025-12-18 Problem mit isr. Zählt zu viel beim losfahren. ISRS abgeändert.
    [DomeControlSTSCI.ino]
2026-01-08 comment schematic
